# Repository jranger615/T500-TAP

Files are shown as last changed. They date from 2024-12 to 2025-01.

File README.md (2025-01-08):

 <H1>T500 TAP Guide for Stock HOT END</h1> 

> [!IMPORTANT]
>All changes ive made are based off previous cfg files using KAMP developed by Trist0ne via https://github.com/Trist0ne/T500-Configuration-Public/tree/main. Please make sure you start with his configurations before you continue or some of this may not work

<br />
I am providing instructions for a 3D Printed OptTap V2.4 RC8 or the CHAOTICLAB Voron Tap V2.0. Below I will list the details of Each
<br />
<br />
<h4>OptTap V2.4 RC8</h4>
https://github.com/VoronDesign/Voron-Tap/tree/main/OptoTap
<ul>
<li>Cheaper </li>
<li>More Assembly</li>
<li>5MM less Y Axis loss over Chaoticlabs</li>
</ul>
<b>Parts Needed:</b>
<br />https://www.amazon.com/dp/B0CSYY24RW
<br />https://www.amazon.com/GBYMIUY-Refrigerator-Magnets-Cylinder-Whiteboard

<h4>CHAOTICLAB Voron Tap V2.0</h4>
<ul>
<li>Precise Engineering</li>
<li>Only 2 Parts to Print</li>
<li>Only Requires 4 m3 Heated Inserts</li>
<li>Loose 25MM of T Axis Room</li>
</ul>

<h2>Wiring the TAP Sensor</h2>
The T500 Stock 4 Pin Probe Connector is as Follows:
<ul>
<li>Brown = 24v </li>
<li>Blue = Ground</li>
<li>Black = Signal </li> 
</ul>

<h4>OptTap V2.4 RC8</h4>
Cut your Sensor Wire off or Order new 4 pin connectos
Stock Fytec Kit Connections
<ul>
<li>Brown Wire > Red Wire </li>
<li>Blue Wire > Black Wire</li>
<li>Black Wire > Green Wire</li>
</ul>

<h4>CHAOTICLAB Voron Tap V2.0</h4>
Cut your Sensor Wire off or Order new 4 pin connectos
<ul>
<li>Brown Wire > Red Wire </li>
<li>Blue Wire > Black Wire</li>
<li>Black Wire > Yellow Wire</li>
</ul>

<h2>X EndStop Sensor Move</h2>
For this modificaiton, move the X end stop sensor from the back of the  X Axis, to the front bottom screw as shown. I used a washer or 2 to help center the tap Adapter extension that will trigger this sensor.


<h2>Voron Tap Assembly</h2>
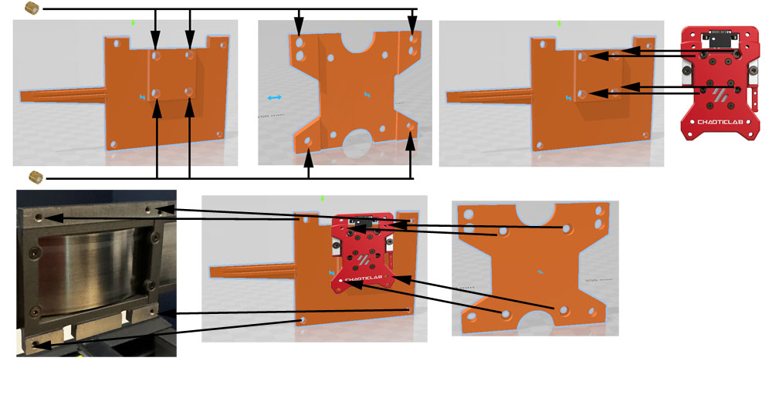
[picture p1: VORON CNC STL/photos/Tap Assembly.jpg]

<h2>HotEnd Changes</h2>
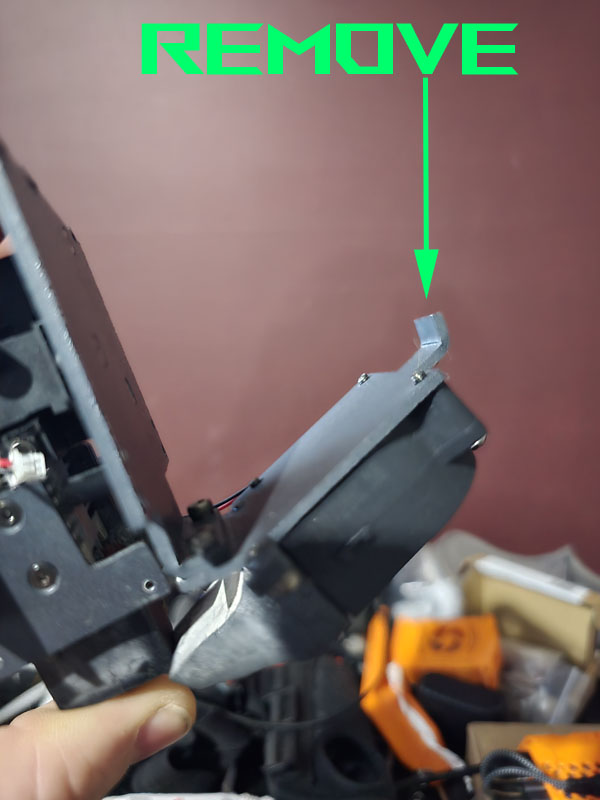
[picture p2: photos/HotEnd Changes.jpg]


<h2>Stepper_y changes</h2>

```ruby
position_endstop: -30 #adjustment for New Offset of Y Axis oddly this brings the hotend to the end of the thermal sheet. You coudl set this to 50 to get to closer to the front of the bed
position_min: -30 #adjustment for New Offset of Y Axis, oddly this brings the hotend to the end of the thermal sheet. You coudl set this to 50 to get to closer to the front of the bed
position_max: 503
```
<h2>probe changes</h2>

```ruby
[probe]
pin:^!PE8  #This was changed from Inital Sensors PE8. We invert the polarity (!) and set pull up (^)
x_offset: 0 #Adjust to 0 as Nozzle is now the sensor
y_offset: 0 #Adjust to 0 as Nozzle is now the sensor
#z_offset: -1.42 #Comment Out and Redo your Z_offset in calibration
speed: 10.0
samples: 3
samples_result: median
sample_retract_dist: 3.0
samples_tolerance: 0.006
samples_tolerance_retries: 10
activate_gcode:
    {% set PROBE_TEMP = 275 %}
    {% set MAX_TEMP = PROBE_TEMP + 5 %}
    {% set ACTUAL_TEMP = printer.extruder.temperature %}
    {% set TARGET_TEMP = printer.extruder.target %}

    {% if TARGET_TEMP > PROBE_TEMP %}
        { action_respond_info('Extruder temperature target of %.1fC is too high, lowering to %.1fC' % (TARGET_TEMP, PROBE_TEMP)) }
        M109 S{ PROBE_TEMP }
    {% else %}
        # Temperature target is already low enough, but nozzle may still be too hot.
        {% if ACTUAL_TEMP > MAX_TEMP %}
            { action_respond_info('Extruder temperature %.1fC is still too high, waiting until below %.1fC' % (ACTUAL_TEMP, MAX_TEMP)) }
            TEMPERATURE_WAIT SENSOR=extruder MAXIMUM={ MAX_TEMP }
        {% endif %}
    {% endif %}
```
<h2>MACRO CHANGES</h2>
Check Your Positioning on these Macros. Mine for instance has G1 X10 Y490 F6000, Y490 is too MUCH with the new config. These will either be in your Macros.CFG or Printer.CFG
<br />

```ruby
[gcode_macro CANCEL_PRINT]
G1 X10 Y475 F6000
```

```ruby
[gcode_macro PAUSE] 
{% set y = params.Y|default(475) %}      #edit to your park position
```

```ruby
[gcode_macro PRINT_END]
G1 X10 Y475 ;Present print
```

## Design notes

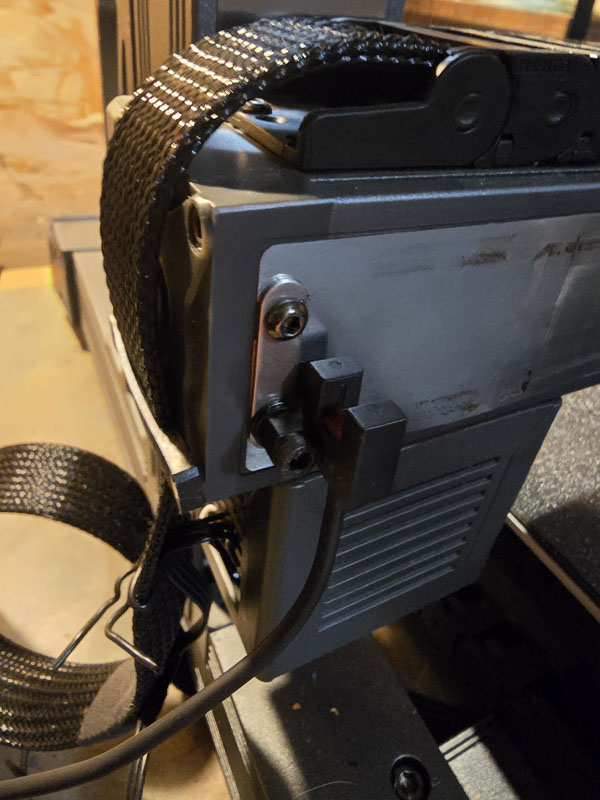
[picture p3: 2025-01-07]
photos/X-EndStop-Sensor.jpg

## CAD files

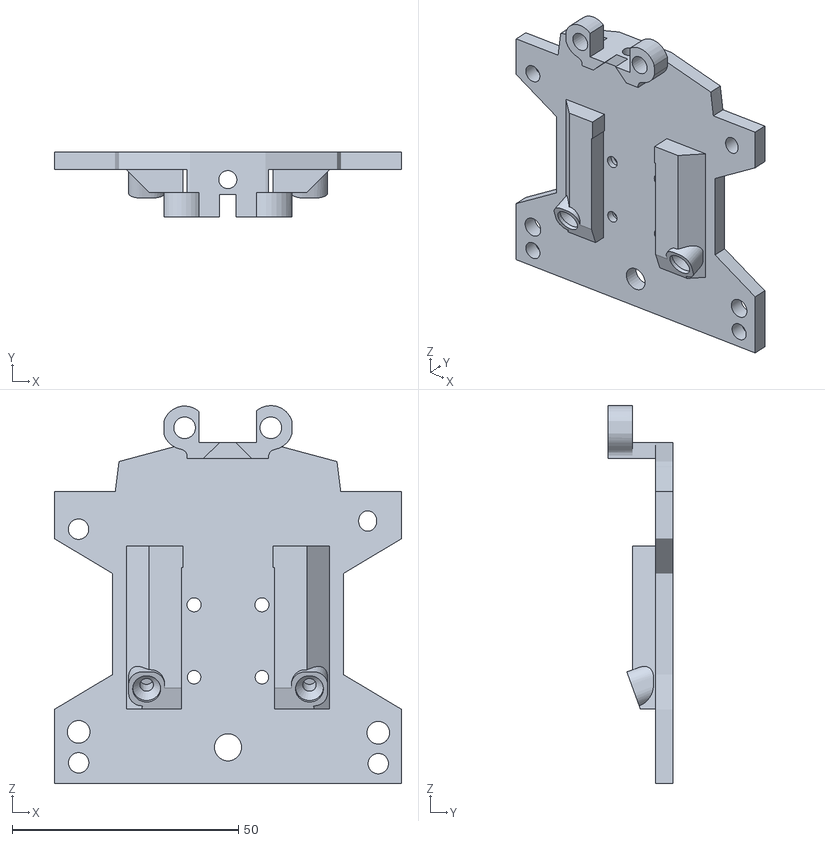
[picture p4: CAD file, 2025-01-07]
STLs/T500 TAP Opto Hotend Adapter.stl
76.8 x 14.4 x 83.6

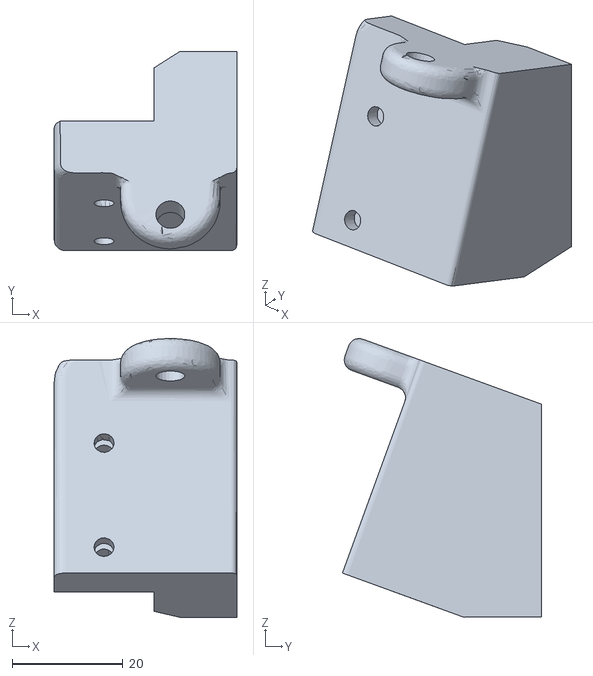
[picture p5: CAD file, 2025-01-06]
VORON CNC STL/t500 runout sensor (4).stl
33.0 x 36.0 x 50.4

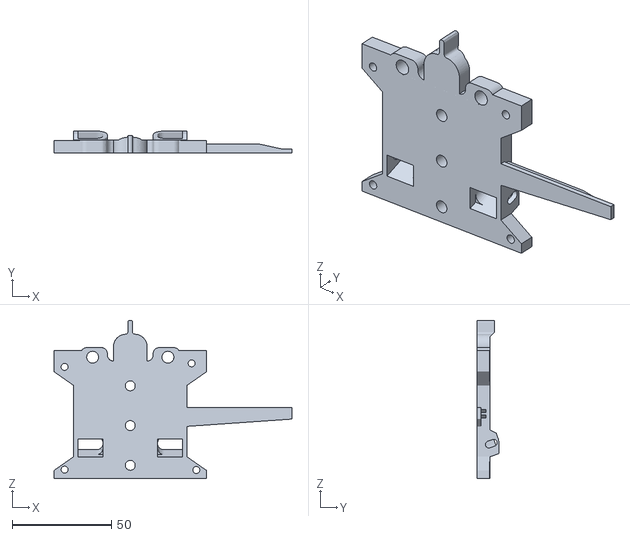
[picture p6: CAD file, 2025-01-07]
STLs/T500 TAP Opto Rail Adapter.stl
119.8 x 11.0 x 79.7

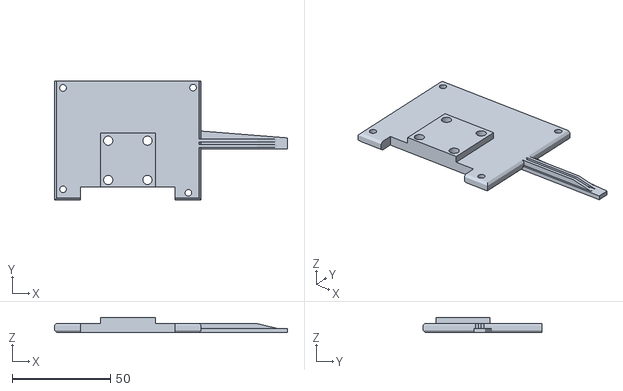
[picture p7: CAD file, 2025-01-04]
VORON CNC STL/T500 TAP Adapter.stl
118.8 x 60.8 x 7.50

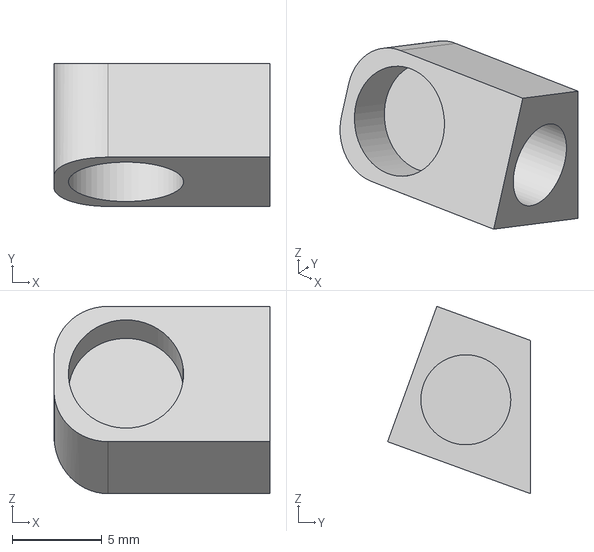
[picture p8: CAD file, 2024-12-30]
STLs/magnet holder R.step
12.0 x 7.94 x 10.4 mm

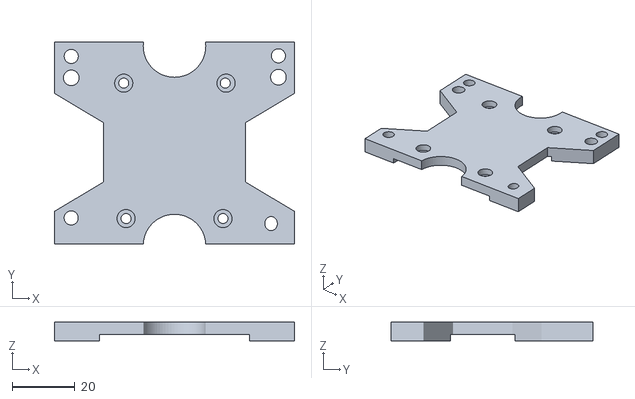
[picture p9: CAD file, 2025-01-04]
VORON CNC STL/T500 HotEnd Adapter.stl
76.8 x 64.5 x 6.00

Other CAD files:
STLs/magnet holder L.step

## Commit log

2024-12-30 Rename T500 TAP HOT END.stl to STLs/T500 TAP HOT END.stl
    [T500 TAP HOT END.stl]
2024-12-30 Rename T500 TAP Rail.stl to STLs/T500 TAP Rail.stl
    [T500 TAP Rail.stl]
2024-12-30 Rename magnet holder L.step to STLs/magnet holder L.step
    [magnet holder L.step]
2024-12-30 Rename magnet holder R.step to STLs/magnet holder R.step
    [magnet holder R.step]
2024-12-30 Rename HotEnd Adapter.stl to VORON CNC STL/HotEnd Adapter.stl
    [HotEnd Adapter.stl]
2024-12-30 Rename Toolhead Adapter Plate.stl to VORON CNC STL/Toolhead Adapter Plate.stl
    [Toolhead Adapter Plate.stl]
2025-01-05 Add files via upload
    Revision to this
    https://www.thingiverse.com/thing:6465090/files
    [t500 runout sensor (2).stl]
2025-01-05 Add files via upload
    This is a revision of https://www.thingiverse.com/thing:6465090/files
    [t500 runout sensor (3).stl]
2025-01-07 Rename Tap Assembly.jpg to VORON CNC STL/photos/Tap Assembly.jpg
